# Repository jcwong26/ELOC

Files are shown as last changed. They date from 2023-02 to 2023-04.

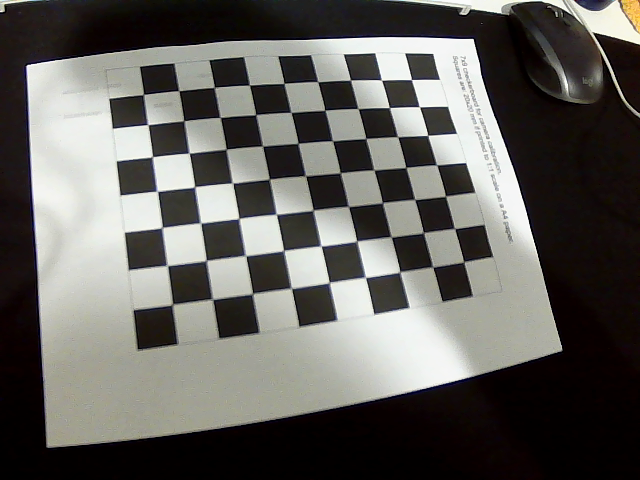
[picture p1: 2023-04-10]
camera_calibration/new_calibration_frames/calibration_frame_17.png

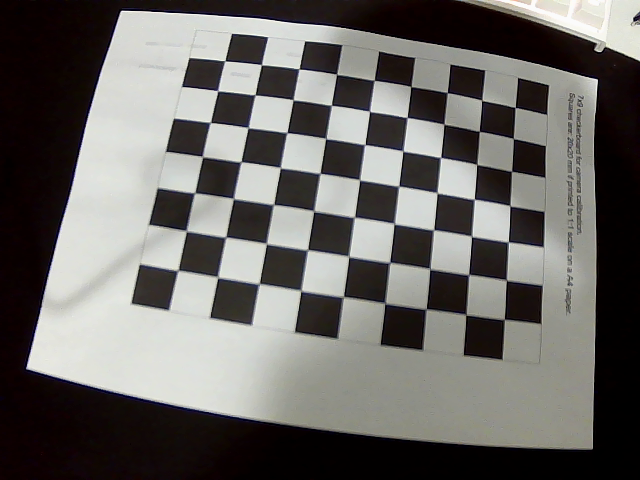
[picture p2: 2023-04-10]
camera_calibration/new_calibration_frames/calibration_frame_25.png

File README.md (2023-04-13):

# Energized Lock Out Container (ELOC)

ELOC is an e-bike storage solution to increase your range, without increasing your weight. With e-bikes becoming increasingly popular as a greener and healthier commuting option, our solution allows for charging of any e-bike so commuters do not have to worry about insufficient charge for their subsequent trips. ELOC features a fully autonomous process to load, lock, and charge your e-bike. With only the addition of a lightweight wireless power transfer adapter, our custom wireless charging technology provides enough power to charge a typical e-bike battery to 80% while securely locked throughout the day.

ELOC is a Capstone Design project made by four Mechatronics Engineering students at the University of Waterloo. 

For more details and a demo video check out our [website](https://mte481-group39-eloc.notion.site/mte481-group39-eloc/Energized-Lock-Out-Container-ELOC-88f4f57b00774851aa3dca28fe943a83)!

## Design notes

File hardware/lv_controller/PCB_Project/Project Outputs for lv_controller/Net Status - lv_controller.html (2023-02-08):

Altium customize

# Net Status Report

Date: | | 2022-11-29
Time: | | 10:16:27 PM
Elapsed Time: | | 00:00:00
Filename: | | C:\Users\dawso\OneDrive - University of Waterloo\4A\MTE481 - FYDP\LV Controller\PCB_Project\lv_controller.PcbDoc
Units: | | mmmils

Nets | Layer | Length
+3V3 | Signal Layers Only | 0mils
+5 | Signal Layers Only | 0mils
GND | Signal Layers Only | 0mils
GPIO17 | Signal Layers Only | 0mils
GPIO18 | Signal Layers Only | 0mils
GPIO21 | Signal Layers Only | 0mils
GPIO33 | Signal Layers Only | 0mils
GPIO34 | Signal Layers Only | 0mils
GPIO35 | Signal Layers Only | 0mils
GPIO36 | Signal Layers Only | 0mils
GPIO45 | Signal Layers Only | 0mils
GPIO46 | Signal Layers Only | 0mils
HSU_RX | Signal Layers Only | 0mils
HSU_TX | Signal Layers Only | 0mils
LIM_SW_1 | Signal Layers Only | 0mils
LIM_SW_2 | Signal Layers Only | 0mils
LIM_SW_3 | Signal Layers Only | 0mils
LIM_SW_4 | Signal Layers Only | 0mils
MCU_BOOT | Signal Layers Only | 0mils
MCU_EN | Signal Layers Only | 0mils
NetC18_2 | Signal Layers Only | 0mils
NetC19_2 | Signal Layers Only | 0mils
NetC20_2 | Signal Layers Only | 0mils
NetC24_2 | Signal Layers Only | 0mils
NetC25_2 | Signal Layers Only | 0mils
NetC26_2 | Signal Layers Only | 0mils
NetC4_1 | Signal Layers Only | 0mils
NetF1_2 | Signal Layers Only | 0mils
NetF2_2 | Signal Layers Only | 0mils
NetL5_1 | Signal Layers Only | 0mils
NetR10_2 | Signal Layers Only | 0mils
NetR11_1 | Signal Layers Only | 0mils
NetR12_1 | Signal Layers Only | 0mils
NetR4_2 | Signal Layers Only | 0mils
NetR7_2 | Signal Layers Only | 0mils
NetR8_1 | Signal Layers Only | 0mils
NetR9_1 | Signal Layers Only | 0mils
NetU1_12 | Signal Layers Only | 0mils
NetU1_15 | Signal Layers Only | 0mils
NetU1_17 | Signal Layers Only | 0mils
NetU1_18 | Signal Layers Only | 0mils
NetU1_19 | Signal Layers Only | 0mils
NetU1_20 | Signal Layers Only | 0mils
NetU1_34 | Signal Layers Only | 0mils
NetU1_35 | Signal Layers Only | 0mils
NetU1_4 | Signal Layers Only | 0mils
NetU1_5 | Signal Layers Only | 0mils
NetU1_6 | Signal Layers Only | 0mils
NetU1_7 | Signal Layers Only | 0mils
RING_LIGHT_DI_3V3 | Signal Layers Only | 0mils
RING_LIGHT_DI_5V | Signal Layers Only | 0mils
SOLENOID_N | Signal Layers Only | 0mils
SOLENOID_P | Signal Layers Only | 0mils
SOLENOID_UNLOCK_HIGH | Signal Layers Only | 0mils
USB_D_N | Signal Layers Only | 0mils
USB_D_P | Signal Layers Only | 0mils
VBUS | Signal Layers Only | 0mils

Back to top

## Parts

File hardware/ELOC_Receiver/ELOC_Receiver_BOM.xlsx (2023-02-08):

Comment | Description | Designator | Footprint | LibRef | Quantity | Arrow Part Number | Manufacturer Part Number | Part Number | PartNumber | Supplier Part Number 1 | Digi-Key_Part_Number_1 | Manufacturer_Part_Number | Manufacturer Part Number 1 | Mouser Part Number | Digi-Key_Part_Number_3 | Digi-Key_Part_Number_2
885012207078 | CAP CER 1UF 25V X7R 0805 | C1, C2, C3, C5 | FP-885012207078-MFG | CMP-207839-000010-1 | 4
C0805C104K1RACAUTO7210 | Capacitor | C4 | C0805 | C0805C104K1RACAUTO7210 | 1 | C0805C104K1RACAUTO7210 |  |  |  |  |  | C0805C104K1RACAUTO7210 |  | 80-C0805C104K1RAUTLR
CL21A106KOQNNNG | CL21 Series 0805 10uF 16V ±10% Tolerance X5R Multilayer Ceramic Chip Capacitor | C6, C7 | FP-CL21-IPC_C | CMP-13271-002240-1 | 2
08055D104KAT2A |  | C8 | CAPC2013X140X50ML20T25 | CMP-2007-04689-1 | 1 |  |  | 08055D104KAT2A
CL21B334KBFNNNE | CAP CER 0.33UF 50V X7R 0805 | C9 | FP-CL21-F-IPC_C | CMP-13271-000003-1 | 1 |  | CL21B334KBFNNNE
CL21A106KOQNNNE | CL21 Series 0805 10uF 16V ±10% Tolerance X5R Multilayer Ceramic Chip Capacitor | C10 | FP-CL21-IPC_B | CMP-2000-06102-2 | 1
CL21A226MQQNNNG | CL21 Series 0805 22uF 6.3V ±20% Tolerance X5R Multilayer Ceramic Chip Capacitor | C11 | FP-CL21-IPC_B | CMP-13271-002967-1 | 1
UCD1K470MNL1GS | Capacitor Polarised | C12, C13 | CAPAE1030X1080N | UCD1K470MNL1GS | 2 | UCD1K470MNL1GS |  |  |  |  |  | UCD1K470MNL1GS |  | 647-UCD1K470MNL1GS
C0805C104K5RACTU | CAP CER 0.1UF 50V X7R 0805 | C14, C23, C24, C25 | CAP0805 | C0805C104K5RACTU | 4 |  |  |  |  | 399-1170-1-ND
C1206C103JAGECAUTO | Capacitor | C15, C16, C17, C18, C19, C20 | CAPC3216X110N | C1206C103JAGECAUTO | 6 | C1206C103JAGECAUTO |  |  |  |  |  | C1206C103JAGECAUTO |  | 80-C1206C103JAGECAUT
GRM21BR71C105KA01L | CAP CER 1UF 16V X7R 0805 | C21 | CAP0805 | GRM21BR71C105KA01L | 1 |  |  |  |  | 490-1691-1-ND
CL21A226MOCLRNC | CAP CER 22UF 16V X5R 0805 | C22 | CAP0805 | CL21A226MOCLRNC | 1 |  |  |  |  | 1276-6780-1-ND
12V | LED GREEN CLEAR 0603 SMD | D1 | FP-150060VS75000-MFG | CMP-1426-00006-5 | 1
5V | LED GREEN CLEAR 0603 SMD | D2 | FP-150060VS75000-MFG | CMP-1426-00006-5 | 1
3V3 | LED GREEN CLEAR 0603 SMD | D3 | FP-150060VS75000-MFG | CMP-1426-00006-5 | 1
1SMB5947BT3G | 3 W Zener Voltage Regulator, 2-Pin SMB, Pb-Free, Tape and Reel | D4, D5, D6 | ONSC-SMB-2-403A-03_H_V | CMP-1060-00168-1 | 3 |  |  |  | 1SMB5947BT3G
MBR5U100-TP | Schottky Diode | D7, D12 | MBR5U100TP | MBR5U100-TP | 2 |  |  |  |  |  |  | MBR5U100-TP
STPS4S200UFN | Schottky Diode | D8, D9, D10, D11, D13, D14, D15, D16 | SODFL5436X110N | STPS4S200UFN | 8 | STPS4S200UFN |  |  |  |  |  | STPS4S200UFN |  | 511-STPS4S200UFN
D_PMEG3050EP,115 | DIODE SCHOTTKY 360mV 30V 5A | D17 | SOD-128 | D_PMEG3050EP,115 | 1
MP4541GN-Z | Integrated Circuit | IC1 | SOIC127P600X170-9N | MP4541GN-Z | 1 |  |  |  |  |  |  | MP4541GN-Z |  | 946-MP4541GN-Z
AS78L05RTR-E1 | Integrated Circuit | IC2 | DIODES_SOT-89 | AS78L05RTR-E1 | 1 | AS78L05RTR-E1 |  |  |  |  |  | AS78L05RTR-E1 |  | 621-AS78L05RTR-E1
691137710002 | Series 1377 - 5.00 mm Horizontal Entry with Pressure Clamp WR-TBL, 2 pin | J1, J2 | 691137710002 | CMP-1502-03324-1 | 2 |  |  | 691137710002
USB4105-GF-A | No Description Available | J3 | USB4105_GCT | USB4105-GF-A | 1 |  |  |  |  |  | 2073-USB4105-GF-ACT-ND | USB4105-GF-A |  |  | 2073-USB4105-GF-ATR-ND | 2073-USB4105-GF-ADKR-ND
61301611821 | THT Vertical Socket Header WR-PHD, Pitch 2.54 mm, Single Row, 16 pins | J4 | 61301611821 | CMP-1502-01343-1 | 1 |  |  | 61301611821
ALQ112 | LQ Relays, 12 V Coil Voltage, 400 mW Nominal Operating Power, -40 to 85 degC, 5-Pin LQ, Carton, Case, RoHS | K1 | PNSC-LQ-5-2000x1000x1600_V | CMP-1503-00193-1 | 1 |  |  |  | ALQ112
LBR2518T100K | SMD Inductors 10uH ±10% 0.235A 0.247Ω 1007 | L1 | FP-LB2518-1_8-0_2-IPC_A | CMP-14484-000483-1 | 1
SDR1307-180ML | Inductor | L2 | SDR1307-220ML | SDR1307-180ML | 1 | SDR1307-180ML |  |  |  |  |  | SDR1307-180ML |  | 652-SDR1307-180ML
T2N7002BK,LM | MOSFET (N-Channel) | Q1 | TBAT54CLM | T2N7002BK,LM | 1 | T2N7002BK,LM |  |  |  |  |  | T2N7002BK,LM |  | 757-T2N7002BKLM
RMCF0805JT10K0 | 10kΩ ±5% 0.125W 0805 Thick Film Chip Resistor AEC-Q200 compliant | R1, R7 | FP-RMCF0805-IPC_A | CMP-26527-002663-1 | 2
CRCW080580K6FKEA | RES Thick Film, 80.6kΩ, 1%, 0.125W, 100ppm/°C, 0805 | R2 | FP-CRCW0805-e3-IPC_A | CMP-2001-04127-2 | 1
RMCF0805FT110K | 110kΩ ±1% 0.125W 0805 Thick Film Chip Resistor AEC-Q200 compliant | R3 | FP-RMCF0805-IPC_C | CMP-26527-000712-1 | 1
RNCP0805FTD1K00 | 1kΩ ±1% 0.25W 0805 High Power Anti-Sulfur Thin Film Chip Resistor | R4, R5, R6 | FP-RNCP0805-MFG | CMP-26527-001902-1 | 3
SHUNT | Resistor | R8 | RESC6434X90N | CRA2512-FZ-R010ELF | 1 | CRA2512-FZ-R010ELF |  |  |  |  |  | CRA2512-FZ-R010ELF |  | 652-CRA2512FZR010ELF
SMF51K0JT | RES SMD 1K OHM 5% 5W 5329 | R9, R10 | FP-SMF5-MFG | CMP-03211-011405-1 | 2
RC0805FR-0710KL | RES SMD 10K OHM 1% 1/8W 0805 | R11, R16, R17, R18 | RES0805 | RC0805FR-0710KL | 4 |  |  |  |  | 311-10.0KCRCT-ND
CRCW08055K10FKEA | RES Thick Film, 5.1kΩ, 1%, 0.125W, 100ppm/°C, 0805 | R12, R13 | FP-CRCW0805-e3-MFG | CMP-2001-04024-2 | 2
RC0805FR-07267KL |  | R14, R15 | RESC2013X60X35NL10T20 | CMP-2001-01033-1 | 2 |  |  | RC0805FR-07267KL
RESET | Tactile Button_3X6X2 | S1 | Tactile_Button_3X6X2 | Tactile Button_3X6X2 | 1
BOOT | Tactile Button_3X6X2 | S2 | Tactile_Button_3X6X2 | Tactile Button_3X6X2 | 1
GND | PC TEST POINT MINIATURE WHITE | TP1 | TESTPOINT_LOOP | TESTPOINT_LOOP | 1 |  |  |  |  | 36-5002-ND |  |  | 5002
12V | PC TEST POINT MINIATURE WHITE | TP2 | TESTPOINT_LOOP | TESTPOINT_LOOP | 1 |  |  |  |  | 36-5002-ND |  |  | 5002
5V | PC TEST POINT MINIATURE WHITE | TP3 | TESTPOINT_LOOP | TESTPOINT_LOOP | 1 |  |  |  |  | 36-5002-ND |  |  | 5002
3V3 | PC TEST POINT MINIATURE WHITE | TP4 | TESTPOINT_LOOP | TESTPOINT_LOOP | 1 |  |  |  |  | 36-5002-ND |  |  | 5002
AZ1117IH-3.3TRG1 | IC REG LINEAR 3.3V 1A SOT223 | U1 | FP-SOT223-IPC_B | CMP-12756-000043-1 | 1
INA180A1IDBVR | IC CURR SENSE 1 CIRCUIT SOT23-5 | U2 | FP-DBV0005A-IPC_A | CMP-04895-000140-1 | 1
ESP32-S2-SOLO-U-N4 | WiFi Modules - 802.11 SMD module, ESP32-S2, 4 MB SPI flash, IPEX antenna | U3 | ESP32S2SOLOUN4 | ESP32-S2-SOLO-U-N4 | 1 |  |  |  |  |  |  | ESP32-S2-SOLO-U-N4 |  | 356-ESP32-S2-SOLOUN4
TC33X-2-203E | Variable Resistor | VR1 | TC33X2503E | TC33X-2-203E | 1 | TC33X-2-203E |  |  |  |  |  | TC33X-2-203E |  | 652-TC33X-2-203E

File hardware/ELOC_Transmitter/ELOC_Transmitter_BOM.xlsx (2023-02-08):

Comment | Description | Designator | Footprint | LibRef | Quantity | Arrow Part Number | Digi-Key_Part_Number_1 | Digi-Key_Part_Number_2 | Digi-Key_Part_Number_3 | Manufacturer Part Number | Manufacturer Part Number 1 | Manufacturer_Part_Number | Mouser Part Number | Part Number | Supplier Part Number 1
885012207078 | CAP CER 1UF 25V X7R 0805 | C1, C2 | FP-885012207078-MFG | CMP-207839-000010-1 | 2
C0805C104K1RACAUTO7210 | Capacitor | C3, C4 | C0805 | C0805C104K1RACAUTO7210 | 2 | C0805C104K1RACAUTO7210 |  |  |  |  |  | C0805C104K1RACAUTO7210 | 80-C0805C104K1RAUTLR
C1206C103JAGECAUTO | Capacitor | C5, C6, C7, C8, C9, C10 | CAPC3216X110N | C1206C103JAGECAUTO | 6 | C1206C103JAGECAUTO |  |  |  |  |  | C1206C103JAGECAUTO | 80-C1206C103JAGECAUT
C0805C104K5RACTU | CAP CER 0.1UF 50V X7R 0805 | C11, C14, C17, C18, C30, C32 | CAP0805 | C0805C104K5RACTU | 6 |  |  |  |  |  |  |  |  |  | 399-1170-1-ND
860010573007 | Capacitor Polarised | C12, C13, C21, C22, C23 | CAPPRD250W52D630H1250 | 860010573007 | 5 |  |  |  |  |  |  | 860010573007 | 710-860010573007
CL21A226MOCLRNC | CAP CER 22UF 16V X5R 0805 | C15, C24, C29, C31 | CAP0805 | CL21A226MOCLRNC | 4 |  |  |  |  |  |  |  |  |  | 1276-6780-1-ND
CL21B334KBFNNNE | CAP CER 0.33UF 50V X7R 0805 | C16, C20 | FP-CL21-F-IPC_C | CMP-13271-000003-1 | 2 |  |  |  |  | CL21B334KBFNNNE
08055D104KAT2A |  | C19 | CAPC2013X140X50ML20T25 | CMP-2007-04689-1 | 1 |  |  |  |  |  |  |  |  | 08055D104KAT2A
CL21B472KBANNNC | CL21 Series 0805 4.7nF 50V ±10% Tolerance X7R Multilayer Ceramic Chip Capacitor | C25 | FP-CL21-IPC_A | CMP-13271-001405-1 | 1
CL21A106KOQNNNE | CL21 Series 0805 10uF 16V ±10% Tolerance X5R Multilayer Ceramic Chip Capacitor | C26 | FP-CL21-IPC_B | CMP-2000-06102-2 | 1
CL21A226MQQNNNG | CL21 Series 0805 22uF 6.3V ±20% Tolerance X5R Multilayer Ceramic Chip Capacitor | C27 | FP-CL21-IPC_B | CMP-13271-002967-1 | 1
GRM21BR71C105KA01L | CAP CER 1UF 16V X7R 0805 | C28 | CAP0805 | GRM21BR71C105KA01L | 1 |  |  |  |  |  |  |  |  |  | 490-1691-1-ND
1N4148WS | DIODE GEN PURP 75V 150MA SOD323F | D1, D2, D3, D4, D5, D6 | FP-477AB-IPC_C | CMP-07163-000040-1 | 6
150060VS75000 | LED GREEN CLEAR 0603 SMD | D7, D10, D11, D12 | FP-150060VS75000-MFG | CMP-1426-00006-5 | 4
SK86L-TP | Schottky Diode | D8, D9 | DIOM7959X262N | SK86L-TP | 2 | SK86L-TP |  |  |  |  |  | SK86L-TP | 833-SK86L-TP
D_PMEG3050EP,115 | DIODE SCHOTTKY 360mV 30V 5A | D13 | SOD-128 | D_PMEG3050EP,115 | 1
NCP5104DR2G | Integrated Circuit | IC1, IC2 | SOIC127P600X175-8N | NCP5104DR2G | 2 | NCP5104DR2G |  |  |  |  |  | NCP5104DR2G | 863-NCP5104DR2G
MP3426DL-LF-Z | Integrated Circuit | IC3 | SON50P300X400X100-15N-D | MP3426DL-LF-Z | 1 |  |  |  |  |  |  | MP3426DL-LF-Z | 946-MP3426DL-LF-Z
AS78L05RTR-E1 | Integrated Circuit | IC4 | DIODES_SOT-89 | AS78L05RTR-E1 | 1 | AS78L05RTR-E1 |  |  |  |  |  | AS78L05RTR-E1 | 621-AS78L05RTR-E1
691137710002 | Series 1377 - 5.00 mm Horizontal Entry with Pressure Clamp WR-TBL, 2 pin | J1, J2 | 691137710002 | CMP-1502-03324-1 | 2 |  |  |  |  |  |  |  |  | 691137710002
USB4105-GF-A | No Description Available | J3 | USB4105_GCT | USB4105-GF-A | 1 |  | 2073-USB4105-GF-ACT-ND | 2073-USB4105-GF-ADKR-ND | 2073-USB4105-GF-ATR-ND |  |  | USB4105-GF-A
PR20203VBNN | CONN HEADER VERT 3POS 2.54MM | J4 | FP-PR20203VBNN-MFG | CMP-77940-000002-1 | 1 |  |  |  |  | PR20203VBNN
SRP1265C-100M | FIXED IND 10UH 12A 18 MOHM SMD | L1 | FP-SRP1265C-MFG | CMP-07248-000045-1 | 1 |  |  |  |  |  |  |  |  | SRP1265C-100M
AOD4184A | MOSFET N-CH 40V 50A TO252 | Q1, Q2, Q3, Q4 | FP-TO252-MFG | CMP-83955-000007-1 | 4
T2N7002BK,LM | MOSFET (N-Channel) | Q5 | TBAT54CLM | T2N7002BK,LM | 1 | T2N7002BK,LM |  |  |  |  |  | T2N7002BK,LM | 757-T2N7002BKLM
RMCF1206FT4R02 | Resistor | R1, R2, R3, R4, R5, R6, R7, R8, R9, R10, R11, R12 | RESC3216X70N | RMCF1206FT4R02 | 12 | RMCF1206FT4R02 |  |  |  |  |  | RMCF1206FT4R02
RNCP0805FTD1K00 | 1kΩ ±1% 0.25W 0805 High Power Anti-Sulfur Thin Film Chip Resistor | R13, R17, R18, R19 | FP-RNCP0805-MFG | CMP-26527-001902-1 | 4
RC0805FR-0710KL | RES SMD 10K OHM 1% 1/8W 0805 | R14, R22, R23, R26, R28, R29 | RES0805 | RC0805FR-0710KL | 6 |  |  |  |  |  |  |  |  |  | 311-10.0KCRCT-ND
SHUNT | Resistor | R15 | RESC6434X90N | CRA2512-FZ-R010ELF | 1 | CRA2512-FZ-R010ELF |  |  |  |  |  | CRA2512-FZ-R010ELF | 652-CRA2512FZR010ELF
ERJ-6ENF6652V |  | R16 | RESC2013X70X40LL20T20 | CMP-2001-00269-1 | 1 |  |  |  |  |  |  |  |  | ERJ-6ENF6652V
ERJ-6ENF1873V |  | R20, R27 | RESC2013X70X40NL20T20 | CMP-1013-00765-2 | 2 |  |  |  |  |  |  |  |  | ERJ-6ENF1873V
RNCP0805FTD12K1 | 12.1kΩ ±1% 0.25W 0805 High Power Anti-Sulfur Thin Film Chip Resistor | R21 | FP-RNCP0805-IPC_B | CMP-26527-004331-1 | 1
CRCW08055K10FKEA | RES Thick Film, 5.1kΩ, 1%, 0.125W, 100ppm/°C, 0805 | R24, R25 | FP-CRCW0805-e3-MFG | CMP-2001-04024-2 | 2
RESET | Tactile Button_3X6X2 | S1 | Tactile_Button_3X6X2 | Tactile Button_3X6X2 | 1
BOOT | Tactile Button_3X6X2 | S2 | Tactile_Button_3X6X2 | Tactile Button_3X6X2 | 1
Bridge 1 | PC TEST POINT MINIATURE WHITE | TP1 | TESTPOINT_LOOP | TESTPOINT_LOOP | 1 |  |  |  |  |  | 5002 |  |  |  | 36-5002-ND
Bridge 2 | PC TEST POINT MINIATURE WHITE | TP2 | TESTPOINT_LOOP | TESTPOINT_LOOP | 1 |  |  |  |  |  | 5002 |  |  |  | 36-5002-ND
Oscillator Out | PC TEST POINT MINIATURE WHITE | TP3 | TESTPOINT_LOOP | TESTPOINT_LOOP | 1 |  |  |  |  |  | 5002 |  |  |  | 36-5002-ND
NOT Oscillator Out | PC TEST POINT MINIATURE WHITE | TP4 | TESTPOINT_LOOP | TESTPOINT_LOOP | 1 |  |  |  |  |  | 5002 |  |  |  | 36-5002-ND
GND | PC TEST POINT MINIATURE WHITE | TP5 | TESTPOINT_LOOP | TESTPOINT_LOOP | 1 |  |  |  |  |  | 5002 |  |  |  | 36-5002-ND
12V | PC TEST POINT MINIATURE WHITE | TP6, TP7 | TESTPOINT_LOOP | TESTPOINT_LOOP | 2 |  |  |  |  |  | 5002 |  |  |  | 36-5002-ND
24V | PC TEST POINT MINIATURE WHITE | TP8, TP9 | TESTPOINT_LOOP | TESTPOINT_LOOP | 2 |  |  |  |  |  | 5002 |  |  |  | 36-5002-ND
5V | PC TEST POINT MINIATURE WHITE | TP10 | TESTPOINT_LOOP | TESTPOINT_LOOP | 1 |  |  |  |  |  | 5002 |  |  |  | 36-5002-ND
3V3 | PC TEST POINT MINIATURE WHITE | TP11 | TESTPOINT_LOOP | TESTPOINT_LOOP | 1 |  |  |  |  |  | 5002 |  |  |  | 36-5002-ND
SN74LVC1G14DBVR | Single Schmitt-Trigger Inverter, DBV0005A, LARGE T&R | U1 | DBV0005A_L | CMP-0859-00030-4 | 1
INA180A1IDBVR | IC CURR SENSE 1 CIRCUIT SOT23-5 | U2 | FP-DBV0005A-IPC_A | CMP-04895-000140-1 | 1
AZ1117IH-3.3TRG1 | IC REG LINEAR 3.3V 1A SOT223 | U3 | FP-SOT223-IPC_B | CMP-12756-000043-1 | 1
ESP32-S2-SOLO-U-N4 | WiFi Modules - 802.11 SMD module, ESP32-S2, 4 MB SPI flash, IPEX antenna | U4 | ESP32S2SOLOUN4 | ESP32-S2-SOLO-U-N4 | 1 |  |  |  |  |  |  | ESP32-S2-SOLO-U-N4 | 356-ESP32-S2-SOLOUN4

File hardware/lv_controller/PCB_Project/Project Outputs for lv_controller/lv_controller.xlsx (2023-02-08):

Comment | Description | Designator | Footprint | LibRef | Quantity
SS2FH10-M3/H, 100V @ 2A | No Description Available | CR1 | CR_10-M3/H_VIS | SS2FH10-M3/H | 1
C1F-8 | C1F 8 (0685F8000-01) | 1206 SMT Fuse | Fast Acting | 8A | F1, F2 | FUSC3215X83N | C1F-8 | 2
USB4105-GF-A | No Description Available | J1 | USB4105_GCT | USB4105-GF-A | 1
RLB0913-2R2K, 2.2uH Inductor, 5.6A |  | L5 | RLB0913-4R7K_BRN | RLB0913-4R7K | 1
NTD14N03RT4G | Power MOSFET, 14 A, 25 V, N-Channel, 3-Pin DPAK, Pb-Free, Tape and Reel | Q1 | ONSC-DPAK-3-369C-01_V | CMP-1058-00361-1 | 1
TS02-66-60-BK-260-LCR-D | 6 x 6 mm, 6 mm Actuator Height, 260 gf, Black, Long Crimped, Through Hole, SPST, Tactile Switch | S1, S2 | SW_TS02-66-60-BK-260-LCR-D | TS02-66-60-BK-260-LCR-D | 2
ESP32-S2-SOLO-U-N4 | WiFi 802.11b/g/n Transceiver Module 2.4GHz PCB Trace + IPEX Surface Mount | U1 | XCVR_ESP32-S2-SOLO-U-N4R2 | ESP32-S2-SOLO-U-N4R2 | 1
TPS566242DRLR | No Description Available | U2 | SOT5x3_DRL_TEX | TPS566242DRLR | 1
BD33HC5WEFJ-E2 | No Description Available | U3 | HTSOP-J8_ROM | BD33HC5WEFJ-E2 | 1
L9958 | Bipolar Motor Driver CMOS SPI PowerSO-16â„¢ | U4, U5 | SOIC127P1420X360-21N | L9958 | 2
TXS0101DCKR | No Description Available | U6 | DCK0006A_N | TXS0101DCKR | 1

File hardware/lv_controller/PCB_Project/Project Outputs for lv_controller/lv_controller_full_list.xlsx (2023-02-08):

Comment | Description | Designator | Footprint | LibRef | Quantity | PartNumber | Application_BuildNumber | DocumentNumber | Manufacturer_Part_Number | Number of contacts
SS2FH10-M3/H, 100V @ 2A | No Description Available | CR1 | CR_10-M3/H_VIS | SS2FH10-M3/H | 1 | SS2FH10-M3/HGICT-ND |  |  | SS2FH10-M3/H
C1F-8 | C1F 8 (0685F8000-01) | 1206 SMT Fuse | Fast Acting | 8A | F1, F2 | FUSC3215X83N | C1F-8 | 2 | 507-1889-1-ND
USB4105-GF-A | No Description Available | J1 | USB4105_GCT | USB4105-GF-A | 1 | 2073-USB4105-GF-ACT-ND |  |  | USB4105-GF-A
RLB0913-2R2K, 2.2uH Inductor, 5.6A |  | L5 | RLB0913-4R7K_BRN | RLB0913-4R7K | 1 | RLB0913-4R7K-ND |  |  | RLB0913-4R7K
NTD14N03RT4G | Power MOSFET, 14 A, 25 V, N-Channel, 3-Pin DPAK, Pb-Free, Tape and Reel | Q1 | ONSC-DPAK-3-369C-01_V | CMP-1058-00361-1 | 1 | NTD14N03RT4GOSCT-ND
TS02-66-60-BK-260-LCR-D | 6 x 6 mm, 6 mm Actuator Height, 260 gf, Black, Long Crimped, Through Hole, SPST, Tactile Switch | S1, S2 | SW_TS02-66-60-BK-260-LCR-D | TS02-66-60-BK-260-LCR-D | 2 | 2223-TS02-66-60-BK-260-LCR-D-ND
ESP32-S2-SOLO-U-N4 | WiFi 802.11b/g/n Transceiver Module 2.4GHz PCB Trace + IPEX Surface Mount | U1 | XCVR_ESP32-S2-SOLO-U-N4R2 | ESP32-S2-SOLO-U-N4R2 | 1 | 1965-ESP32-S2-SOLO-U-N4CT-ND
TPS566242DRLR | No Description Available | U2 | SOT5x3_DRL_TEX | TPS566242DRLR | 1 | 296-TPS566242DRLRCT-ND |  |  | TPS566242DRLR
BD33HC5WEFJ-E2 | No Description Available | U3 | HTSOP-J8_ROM | BD33HC5WEFJ-E2 | 1 | BD33HC5WEFJ-E2CT-ND |  |  | BD33HC5WEFJ-E2
L9958 | Bipolar Motor Driver CMOS SPI PowerSO-16â„¢ | U4, U5 | SOIC127P1420X360-21N | L9958 | 2 | 497-11626-5-ND
TXS0101DCKR | No Description Available | U6 | DCK0006A_N | TXS0101DCKR | 1 | 296-22864-1-ND |  |  | TXS0101DCKR
12V Solenoid Lock |  |  |  |  | 1 | 1528-5065-ND |  |  | 5065
Limit Switch | SWITCH SNAP ACT SPST-NO 3A 125V |  |  |  | 4 | Z6377-ND |  |  | SS-3FL111P-3T

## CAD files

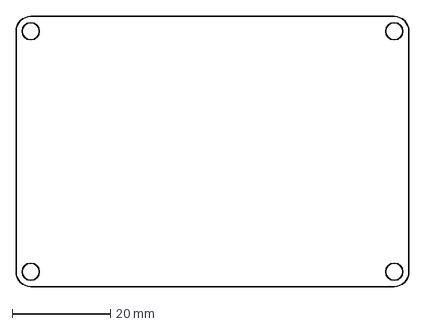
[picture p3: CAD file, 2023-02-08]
hardware/ELOC_Receiver/receiver_board_outline.dxf
80.0 x 55.0 mm

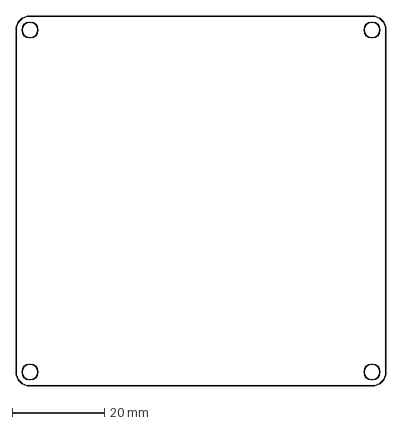
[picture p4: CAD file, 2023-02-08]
hardware/ELOC_Transmitter/transmitter_board_outline.dxf
80.0 x 80.0 mm

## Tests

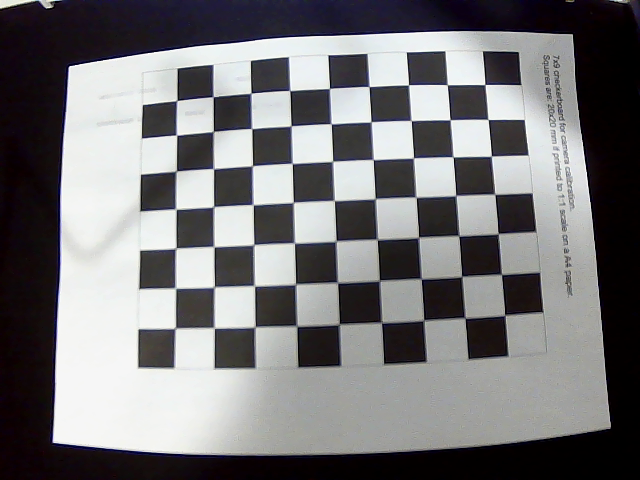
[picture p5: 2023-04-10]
camera_calibration/new_calibration_frames/calibration_frame_18.png

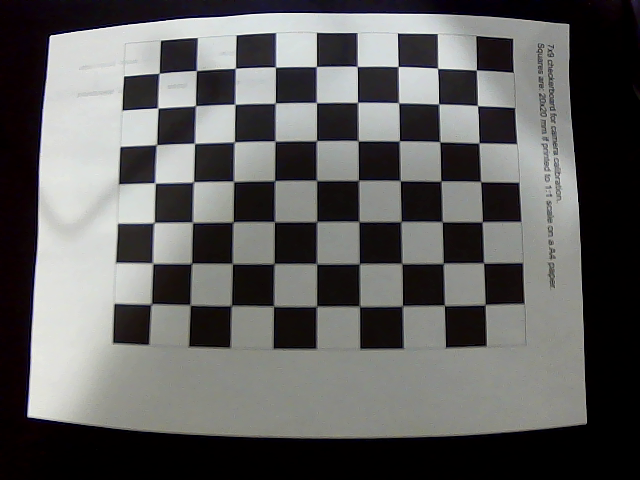
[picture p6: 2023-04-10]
camera_calibration/new_calibration_frames/calibration_frame_10.png

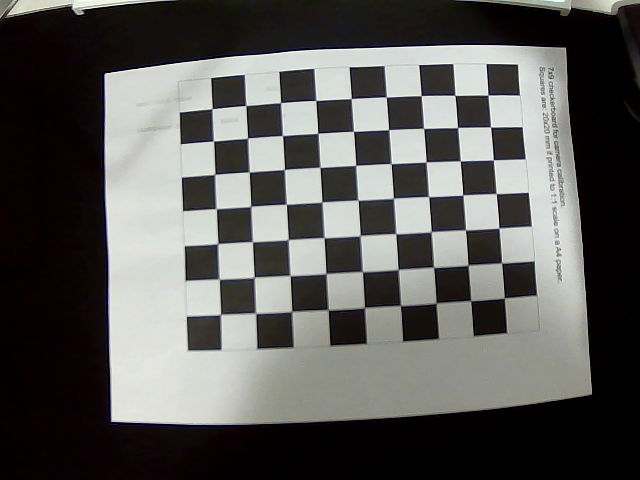
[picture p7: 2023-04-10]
camera_calibration/new_calibration_frames/calibration_frame_21.png

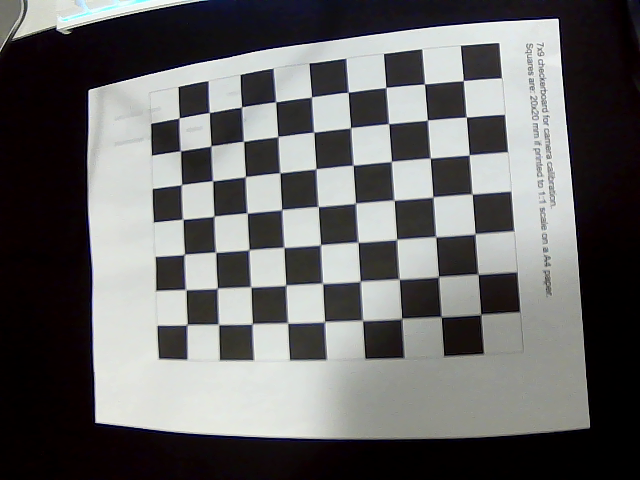
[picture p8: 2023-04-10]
camera_calibration/new_calibration_frames/calibration_frame_23.png

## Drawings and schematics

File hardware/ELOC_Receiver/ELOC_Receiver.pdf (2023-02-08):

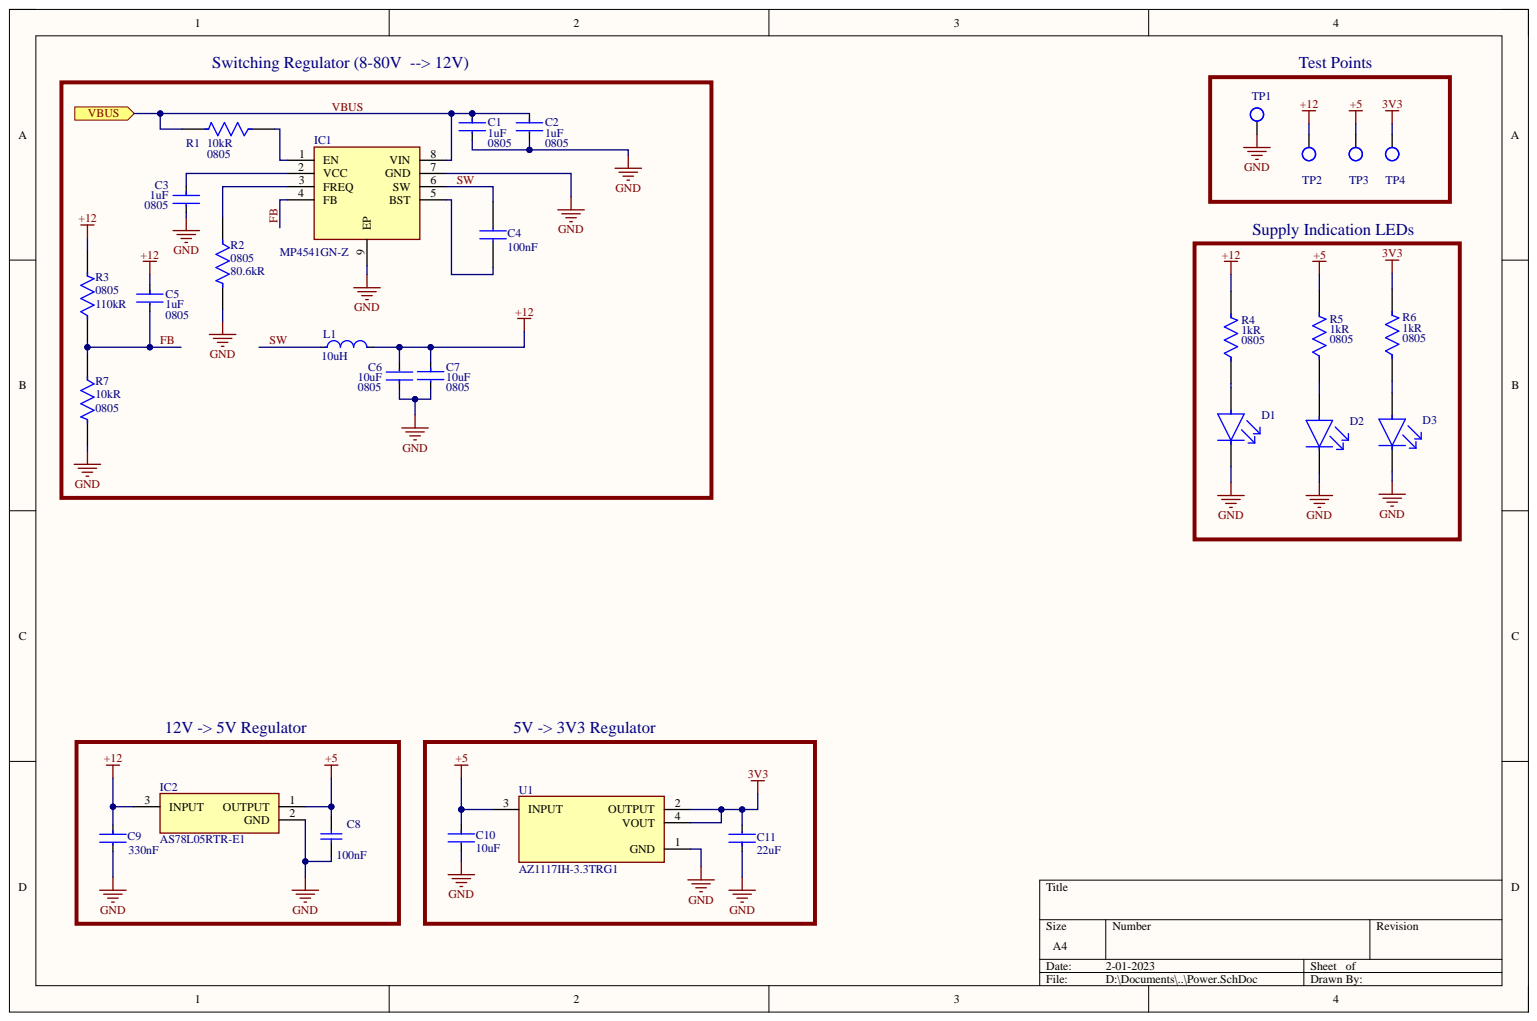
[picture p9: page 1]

3 | | 6 | SW

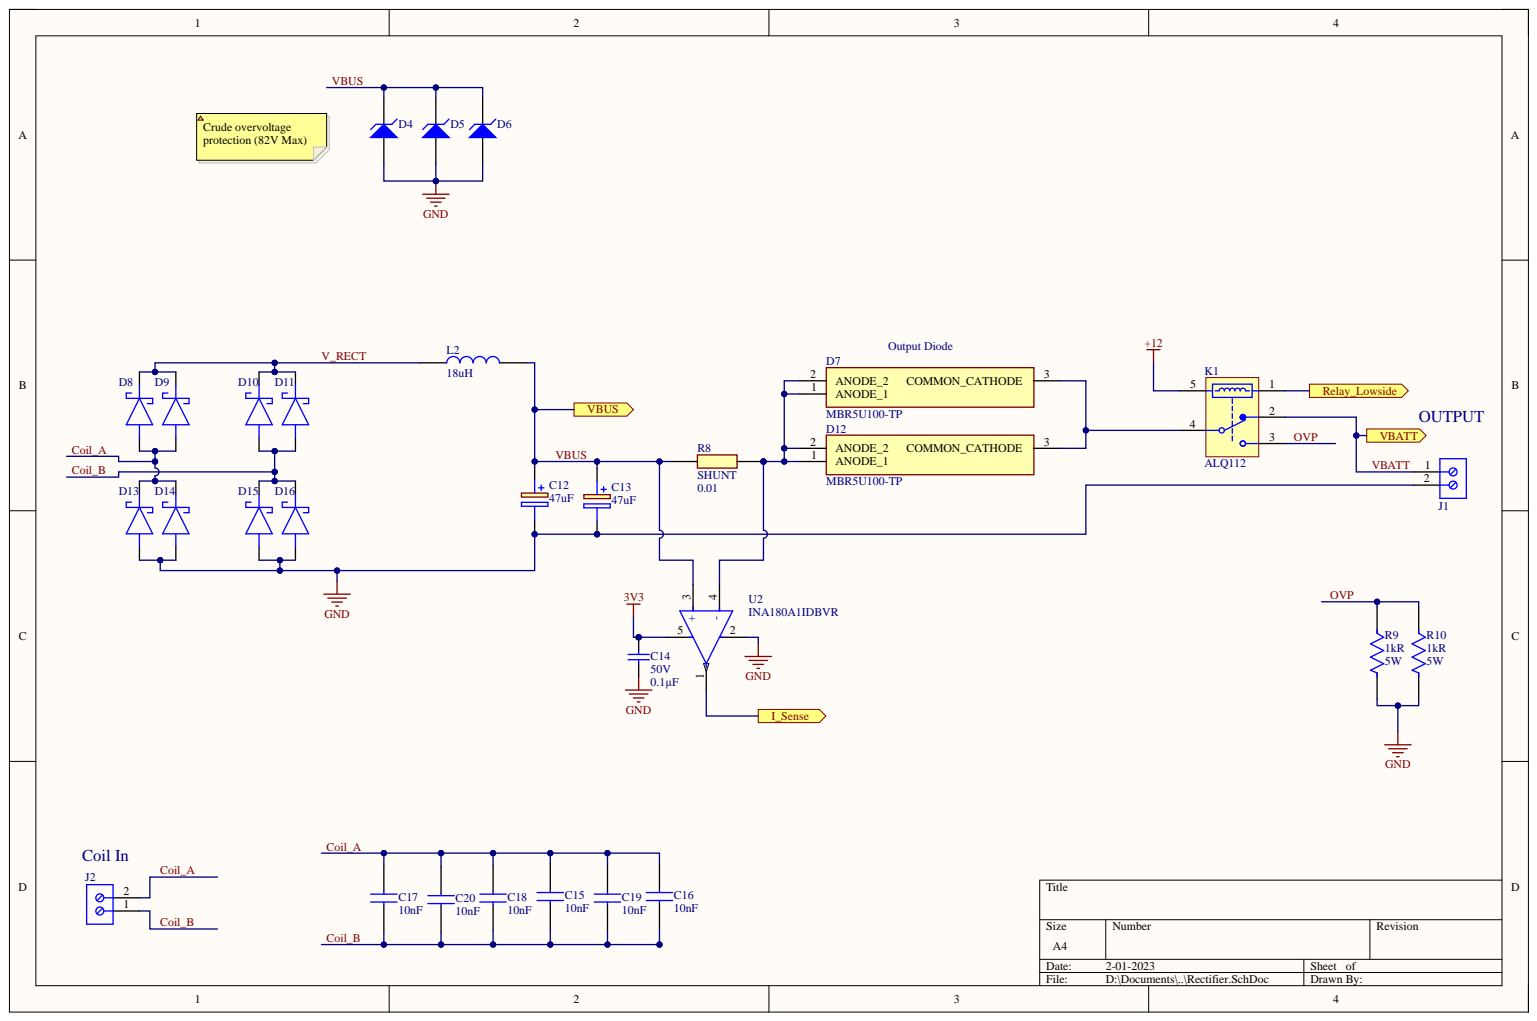
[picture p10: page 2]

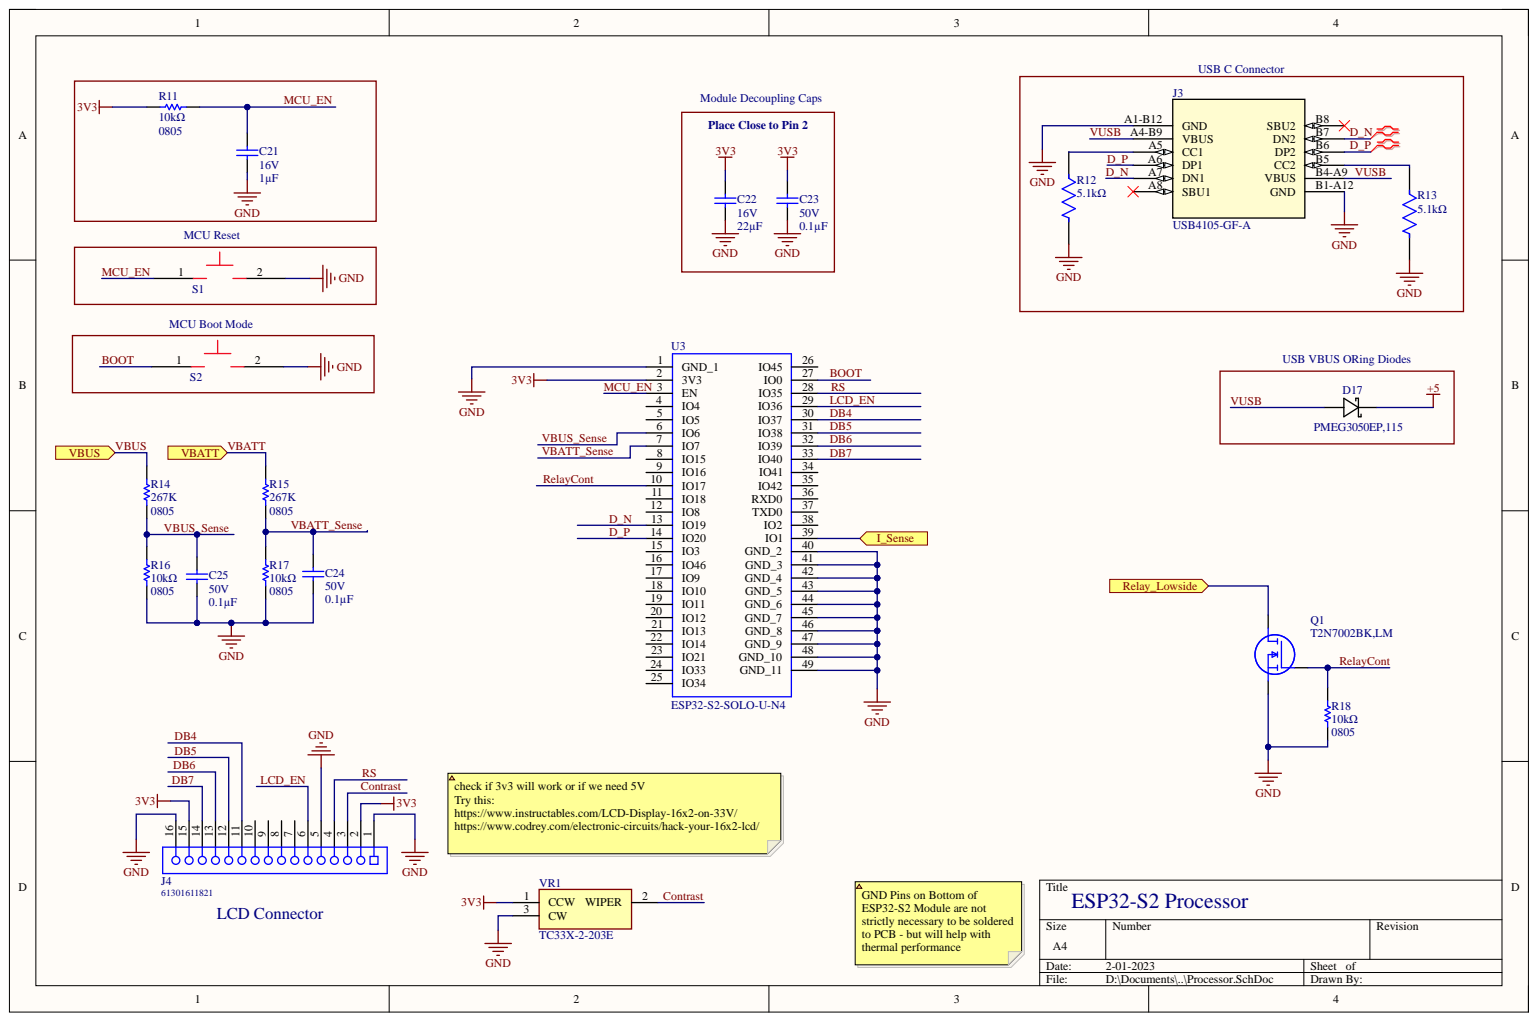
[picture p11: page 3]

Place Close to Pin 2 10kΩ

VBUS_Sense | IO7 7
VBATT_Sense | IO15 8

check if 3v3 will work or if we need 5V
Try this:
https://www.instructables.com/LCD-Display-16x2-on-33V/
https://www.codrey.com/electronic-circuits/hack-your-16x2-lcd/

GND Pins on Bottom of
ESP32-S2 Module are not
strictly necessary to be soldered
to PCB - but will help with
thermal performance

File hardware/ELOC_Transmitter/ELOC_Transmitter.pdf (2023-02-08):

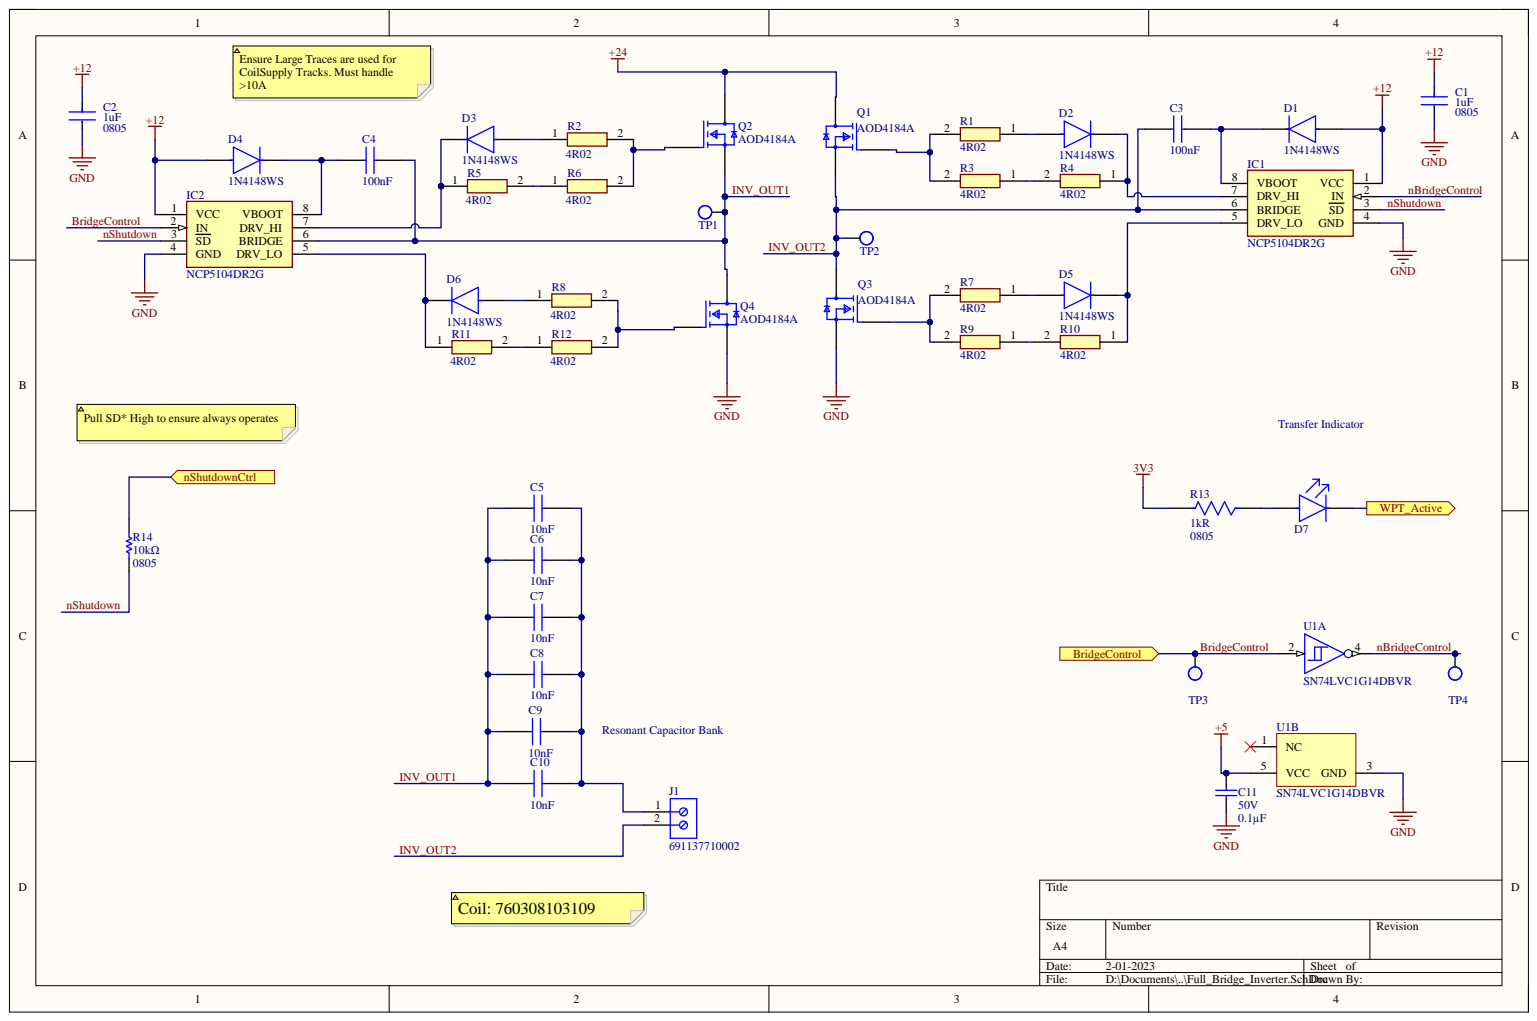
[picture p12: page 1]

Ensure Large Traces are used for
CoilSupply Tracks. Must handle

Pull SD* High to ensure always operates

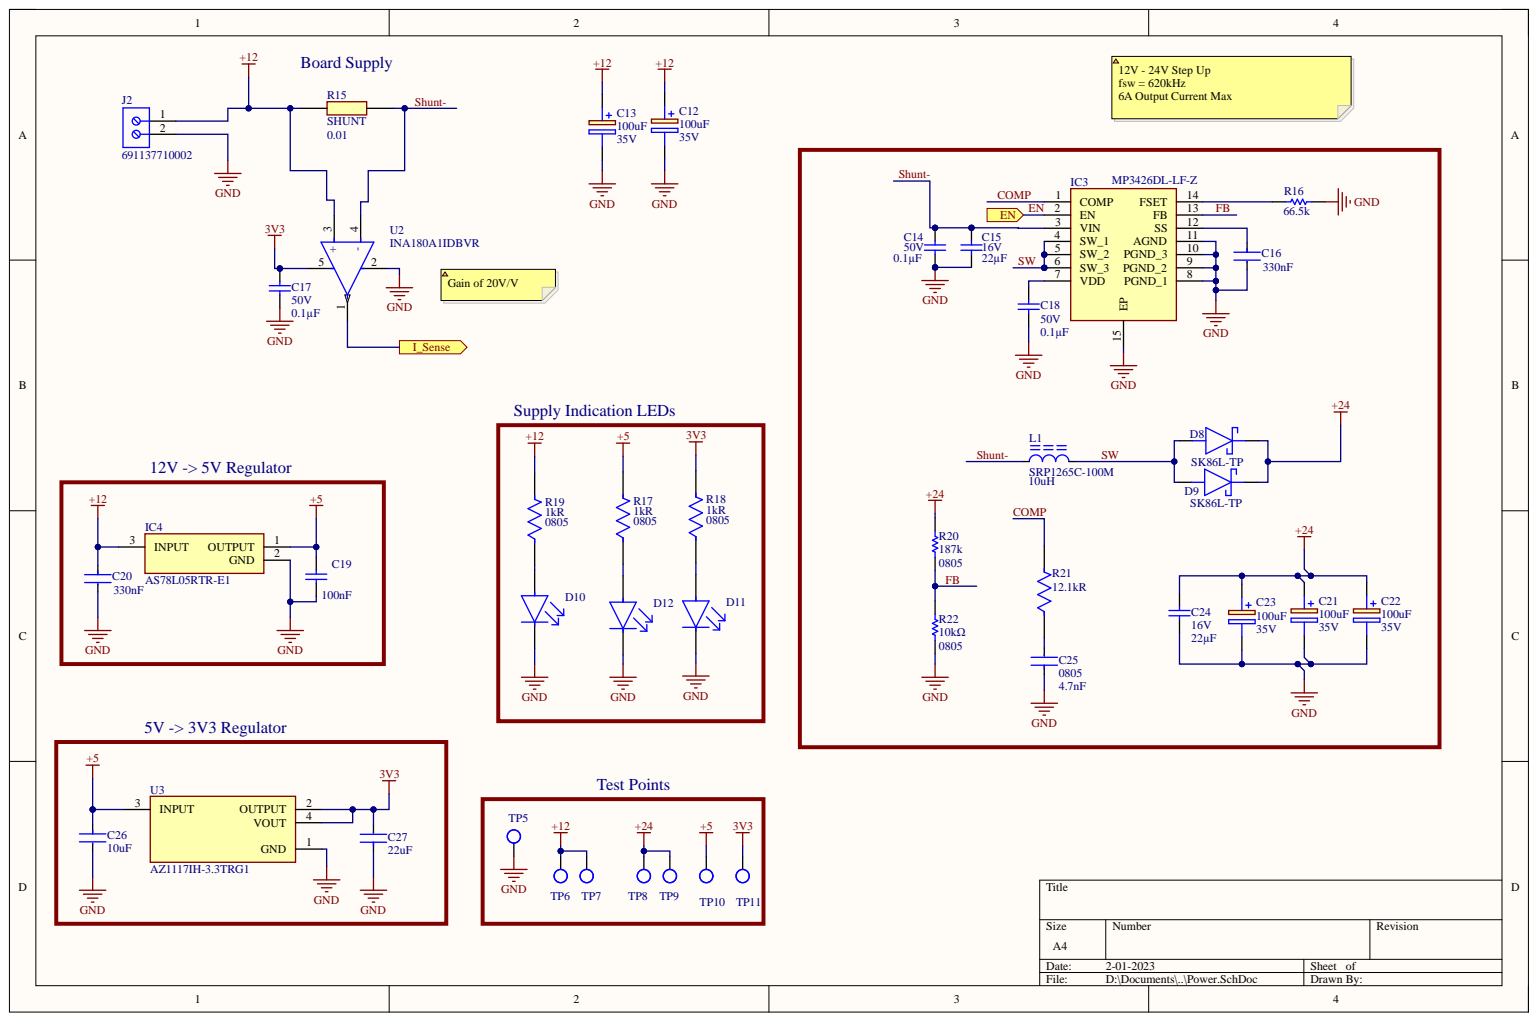
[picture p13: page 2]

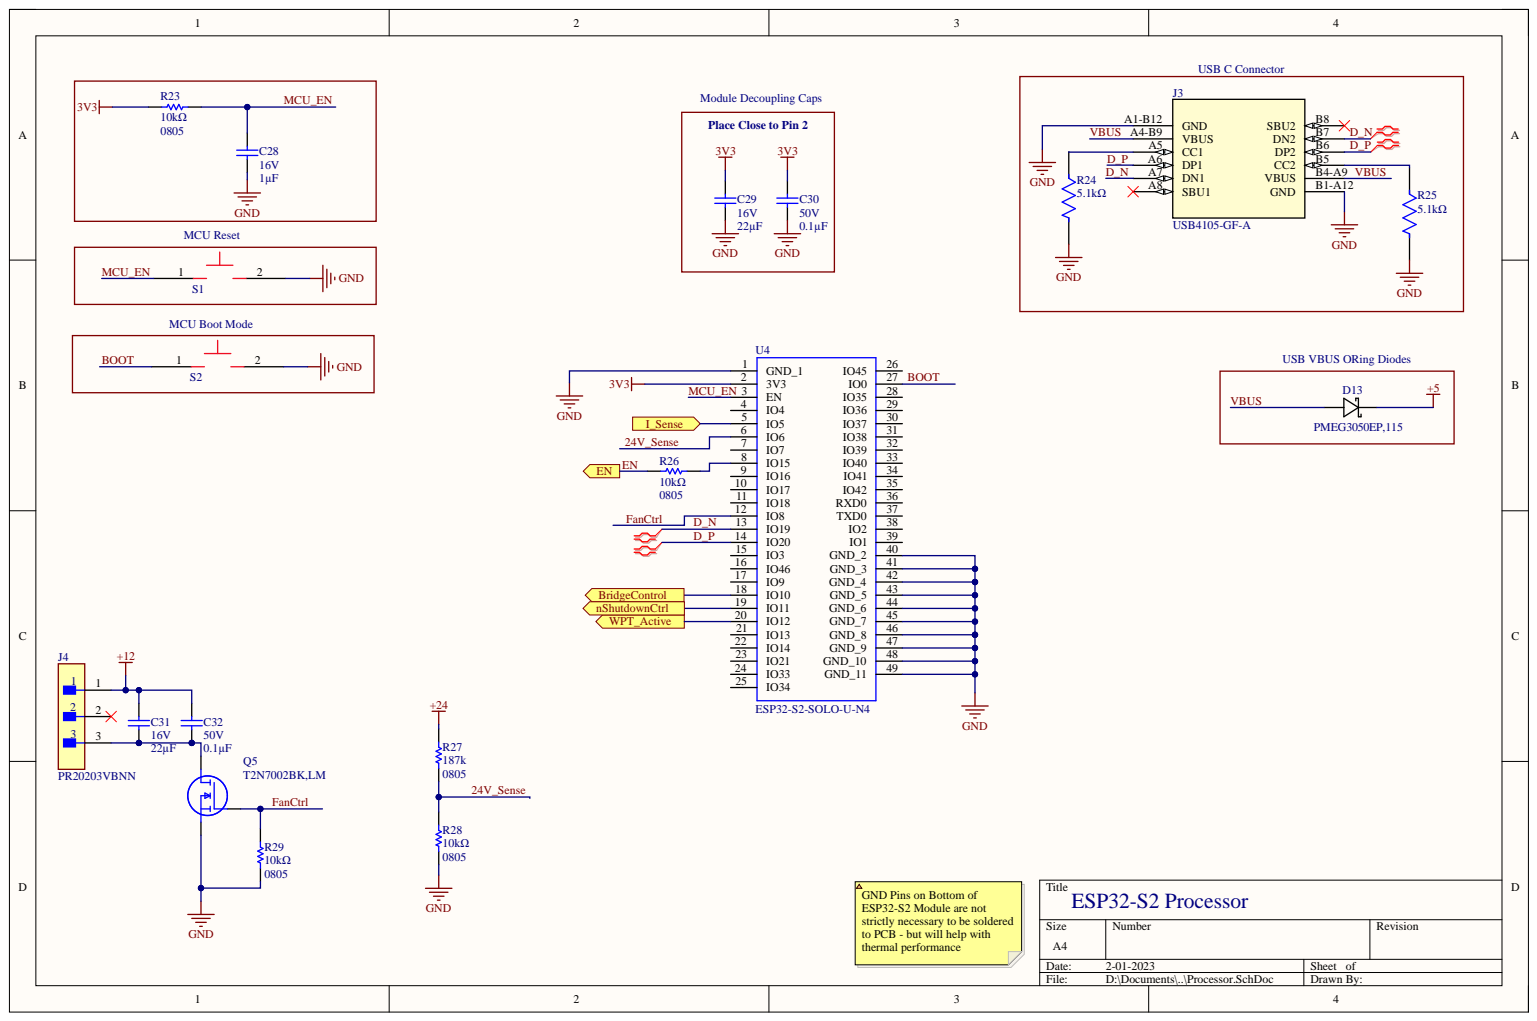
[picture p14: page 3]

Place Close to Pin 2 10kΩ

GND Pins on Bottom of
ESP32-S2 Module are not
strictly necessary to be soldered
to PCB - but will help with
thermal performance

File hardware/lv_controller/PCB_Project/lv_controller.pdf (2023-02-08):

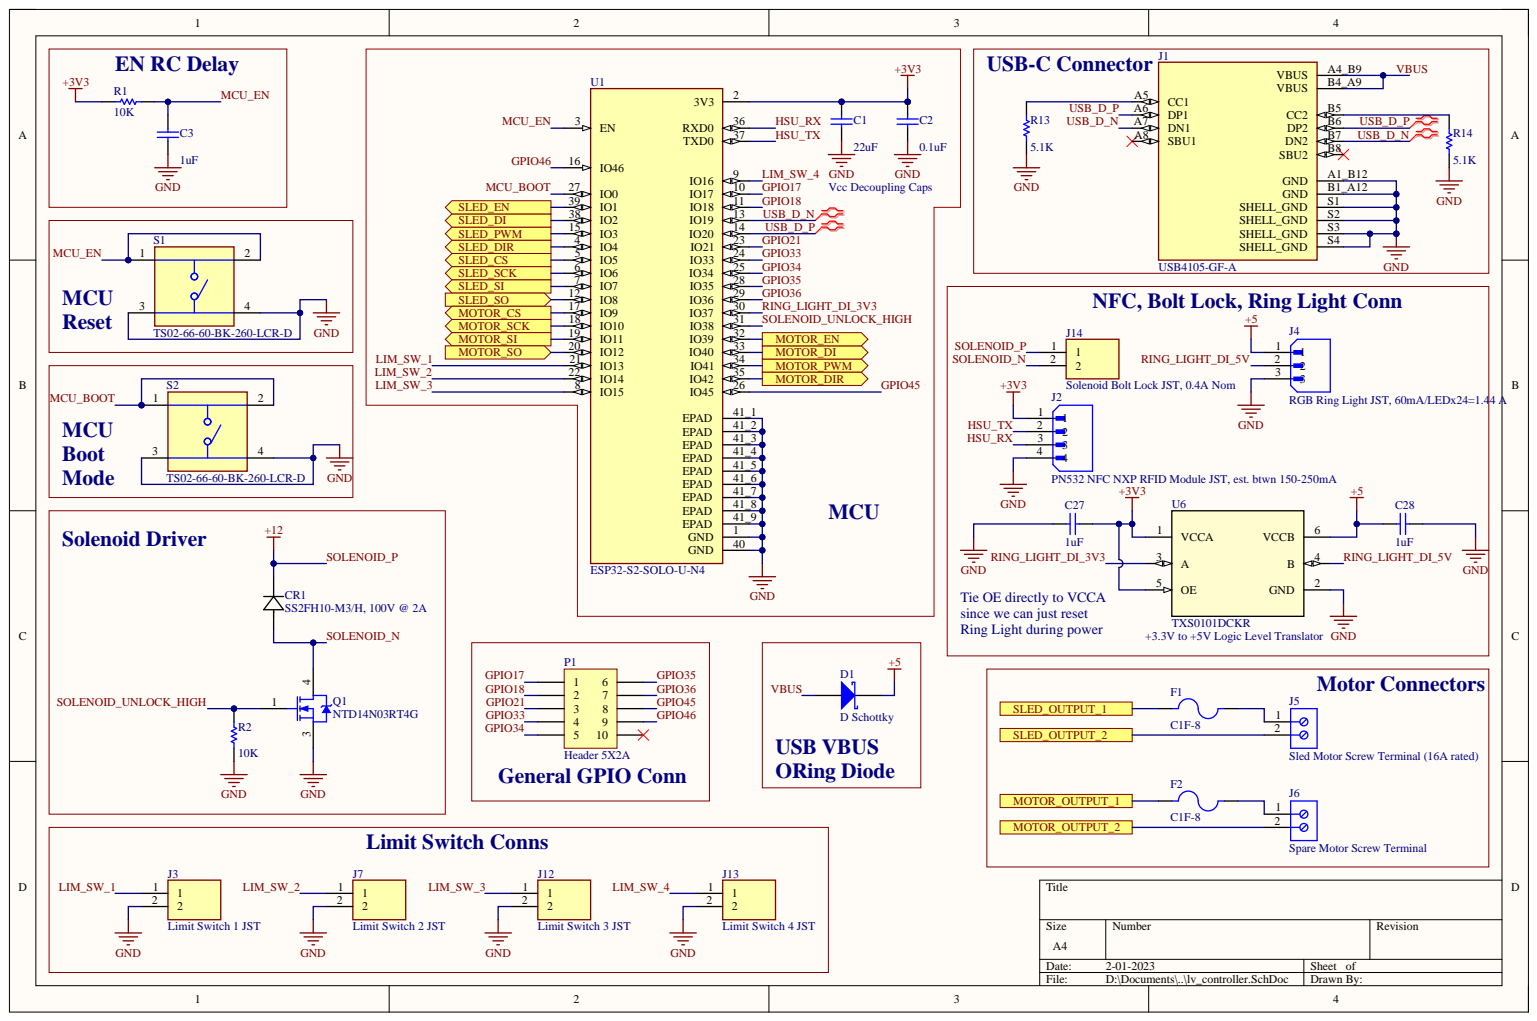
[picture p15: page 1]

NFC, Bolt Lock, Ring Light Conn

RGB Ring Light JST, 60mA/LEDx24=1.44 A

PN532 NFC NXP RFID Module JST, est. btwn 150-250mA

Tie OE directly to VCCA
since we can just reset
Ring Light during power

TXS0101DCKR
+3.3V to +5V Logic Level Translator GND

Sled Motor Screw Terminal (16A rated)

Spare Motor Screw Terminal

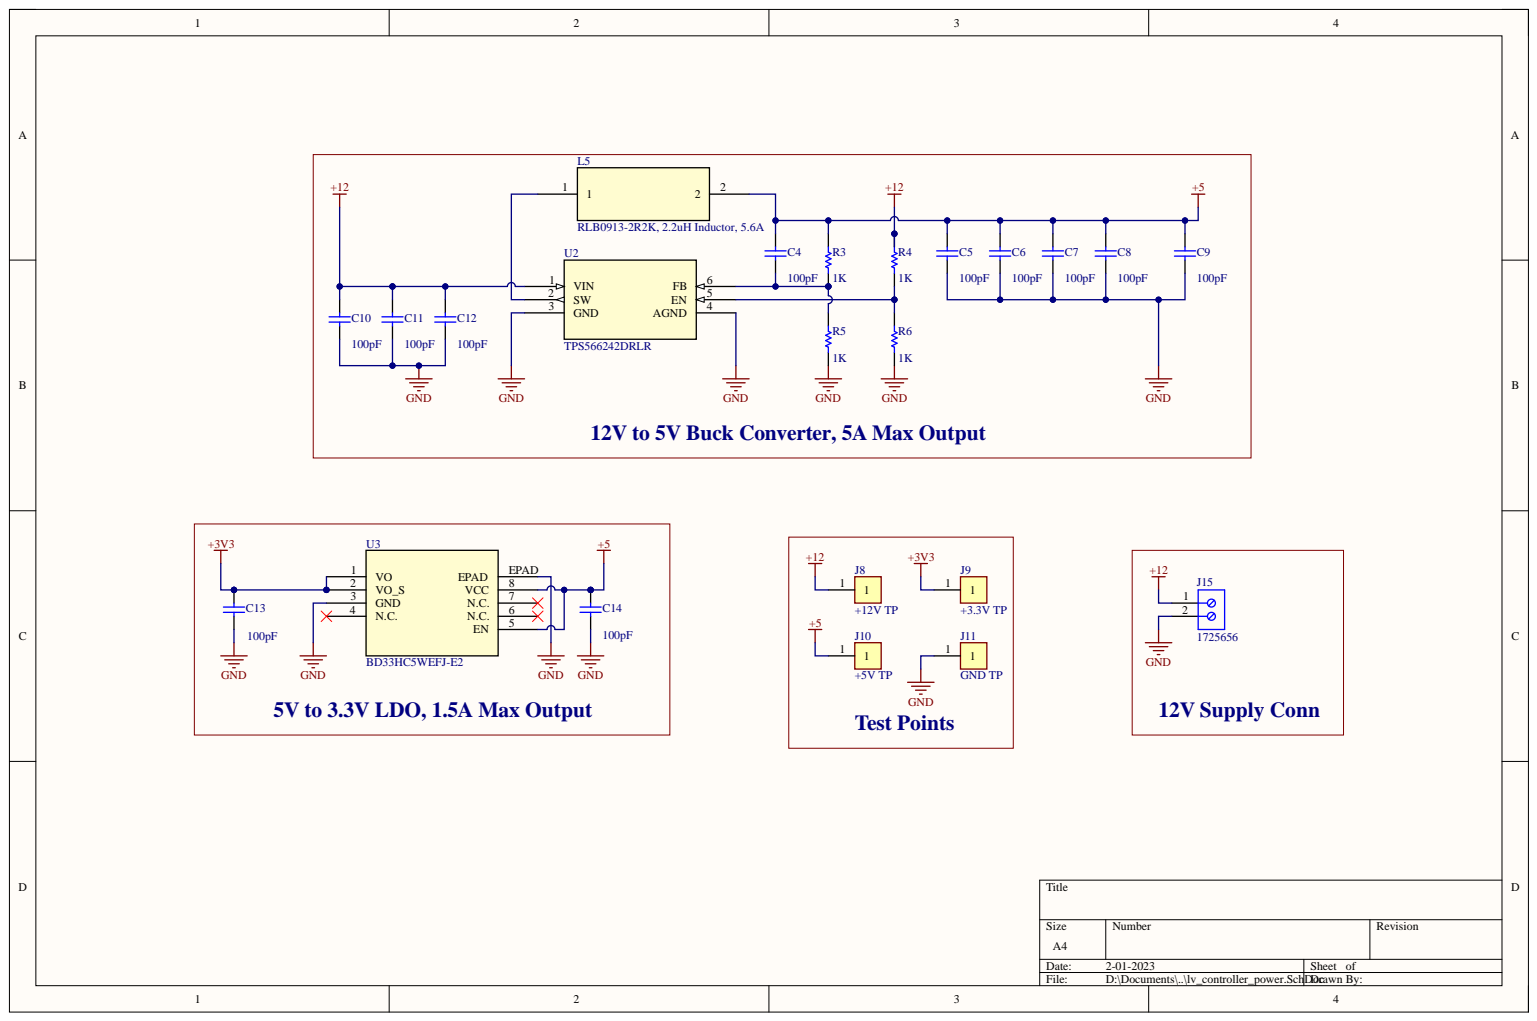
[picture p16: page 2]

12V to 5V Buck Converter, 5A Max Output

5V to 3.3V LDO, 1.5A Max Output

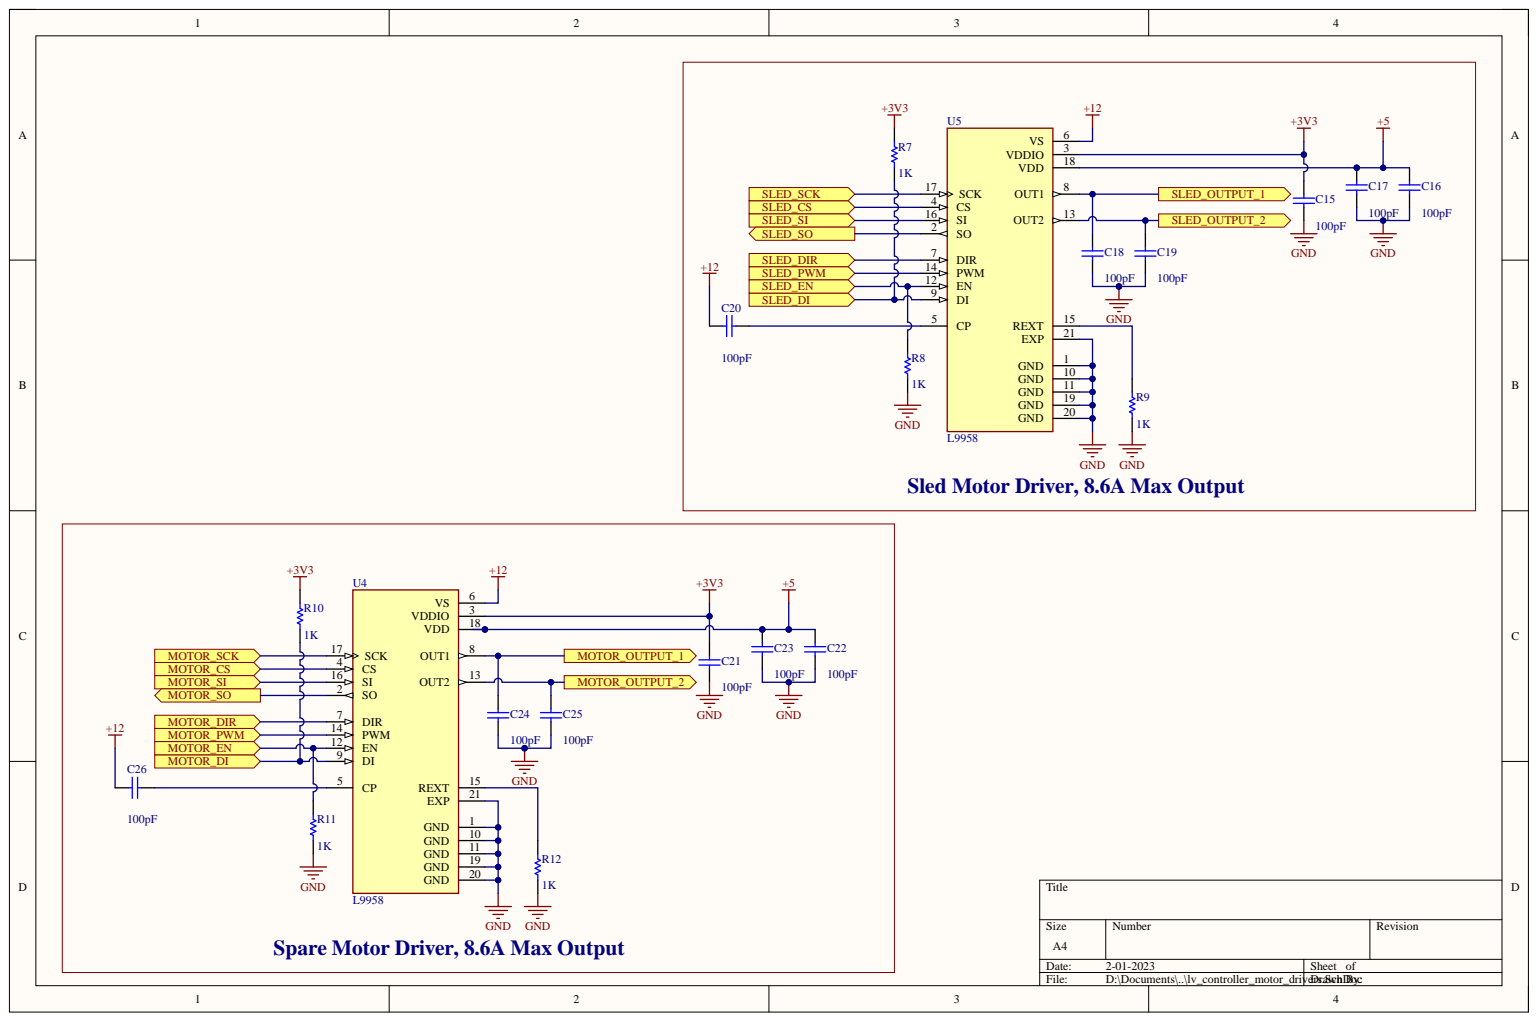
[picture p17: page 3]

Sled Motor Driver, 8.6A Max Output

DI 9 | GND

Spare Motor Driver, 8.6A Max Output

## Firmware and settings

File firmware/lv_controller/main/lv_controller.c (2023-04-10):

#include <stdio.h>
#include <stdbool.h>
#include <string.h>
#include <fcntl.h>

#include "freertos/FreeRTOS.h"
#include "freertos/task.h"
#include "freertos/queue.h"
#include "esp_log.h"
#include "esp_err.h"
#include "pn532.h"
#include "driver/gpio.h"
#include "driver/spi_master.h"
#include "driver/ledc.h"
#include "esp_system.h"
#include "esp_console.h"
#include "linenoise/linenoise.h"
#include "argtable3/argtable3.h"
#include "esp_vfs_cdcacm.h"
#include "nvs.h"
#include "nvs_flash.h"
#include "cmd_nvs.h"
#include "cmd_system.h"

#include "lv_controller.h"
#include "commands.h"
#include "nfc_module.h"
#include "ring_light.h"
#include "limit_switches.h"
#include "state_machine.h"

/* MACROS */
#define SENDER_HOST SPI2_HOST
#define PIN_NUM_MISO 12
#define PIN_NUM_MOSI 7
#define PIN_NUM_CLK 6
#define PIN_NUM_CS 5

/* GLOBALS */
static const char *TAG = "main";
TaskHandle_t nfc_module_task_handle = NULL;
TaskHandle_t state_machine_task_handle = NULL;

/* INITS */
static void init_GPIO(void)
{
    // Set solenoid output
    gpio_set_direction(GPIO_NUM_38, GPIO_MODE_OUTPUT);

    // Set limit switch inputs
    gpio_set_direction(LIM1_GPIO, GPIO_MODE_INPUT); // LIM1
    gpio_pulldown_dis(LIM1_GPIO);
    gpio_pullup_en(LIM1_GPIO);
    gpio_set_intr_type(LIM1_GPIO, GPIO_INTR_NEGEDGE);

    gpio_set_direction(LIM2_GPIO, GPIO_MODE_INPUT); // LIM2
    gpio_pulldown_dis(LIM2_GPIO);
    gpio_pullup_en(LIM2_GPIO);
    gpio_set_intr_type(LIM2_GPIO, GPIO_INTR_NEGEDGE);

    gpio_set_direction(LIM3_GPIO, GPIO_MODE_INPUT); // LIM3
    gpio_pulldown_dis(LIM3_GPIO);
    gpio_pullup_en(LIM3_GPIO);
    gpio_set_intr_type(LIM3_GPIO, GPIO_INTR_NEGEDGE);

    gpio_set_direction(LIM4_GPIO, GPIO_MODE_INPUT); // LIM4
    gpio_pulldown_dis(LIM4_GPIO);
    gpio_pullup_en(LIM4_GPIO);
    gpio_set_intr_type(LIM4_GPIO, GPIO_INTR_NEGEDGE);

    // Set sled control outputs
    gpio_set_direction(GPIO_NUM_1, GPIO_MODE_OUTPUT); // EN
    gpio_set_direction(GPIO_NUM_2, GPIO_MODE_OUTPUT); // DI
    gpio_set_direction(GPIO_NUM_3, GPIO_MODE_OUTPUT); // PWM
    gpio_set_direction(GPIO_NUM_4, GPIO_MODE_OUTPUT); // DIR
}

static void ledc_init(void)
{
    // Prepare and then apply the LEDC PWM timer configuration
    ledc_timer_config_t ledc_timer = {
        .speed_mode = LEDC_MODE,
        .timer_num = LEDC_TIMER_0,
        .duty_resolution = LEDC_TIMER_10_BIT,
        .freq_hz = 1000, // Set output frequency at 5 kHz
        .clk_cfg = LEDC_AUTO_CLK};
    ESP_ERROR_CHECK(ledc_timer_config(&ledc_timer));

    // Prepare and then apply the LEDC PWM channel configuration
    ledc_channel_config_t ledc_channel = {
        .speed_mode = LEDC_MODE,
        .channel = LEDC_CHANNEL_0,
        .timer_sel = LEDC_TIMER_0,
        .intr_type = LEDC_INTR_DISABLE,
        .gpio_num = LEDC_GPIO,
        .duty = 0, // Set duty to 0%
        .hpoint = 0};
    ESP_ERROR_CHECK(ledc_channel_config(&ledc_channel));
}

static void initialize_nvs(void)
{
    esp_err_t err = nvs_flash_init();
    if (err == ESP_ERR_NVS_NO_FREE_PAGES || err == ESP_ERR_NVS_NEW_VERSION_FOUND)
    {
        ESP_ERROR_CHECK(nvs_flash_erase());
        err = nvs_flash_init();
    }
    ESP_ERROR_CHECK(err);
}

static void initialize_console(void)
{
    /* Disable buffering on stdin */
    setvbuf(stdin, NULL, _IONBF, 0);

    /* Minicom, screen, idf_monitor send CR when ENTER key is pressed */
    esp_vfs_dev_cdcacm_set_rx_line_endings(ESP_LINE_ENDINGS_CR);
    /* Move the caret to the beginning of the next line on '\n' */
    esp_vfs_dev_cdcacm_set_tx_line_endings(ESP_LINE_ENDINGS_CRLF);

    /* Enable non-blocking mode on stdin and stdout */
    fcntl(fileno(stdout), F_SETFL, 0);
    fcntl(fileno(stdin), F_SETFL, 0);

    /* Initialize the console */
    esp_console_config_t console_config = {
        .max_cmdline_args = 8,
        .max_cmdline_length = 256,
#if CONFIG_LOG_COLORS
        .hint_color = atoi(LOG_COLOR_CYAN)
#endif
    };
    ESP_ERROR_CHECK(esp_console_init(&console_config));

    /* Configure linenoise line completion library */
    /* Enable multiline editing. If not set, long commands will scroll within
     * single line.
     */
    linenoiseSetMultiLine(1);

    /* Tell linenoise where to get command completions and hints */
    linenoiseSetCompletionCallback(&esp_console_get_completion);
    linenoiseSetHintsCallback((linenoiseHintsCallback *)&esp_console_get_hint);

    /* Set command history size */
    linenoiseHistorySetMaxLen(10);
}

/* REGISTER COMMANDS */
static void register_commands(void)
{
    /* Lock Solenoid */
    esp_console_cmd_t lock_solenoid_cmd = {
        .command = "lock_solenoid",
        .help = "Sets solenoid bolt to locked state",
        .hint = NULL,
        .func = lock_solenoid_comm,
        .argtable = NULL,
    };
    esp_err_t ret = esp_console_cmd_register(&lock_solenoid_cmd);
    if (ret != ESP_OK)
    {
        printf("Error resgistering 'lock_solenoid' command\n");
    }

    /* Unlock Solenoid */
    esp_console_cmd_t unlock_solenoid_cmd = {
        .command = "unlock_solenoid",
        .help = "Sets solenoid bolt to unlocked state",
        .hint = NULL,
        .func = unlock_solenoid_comm,
        .argtable = NULL,
    };
    ret = esp_console_cmd_register(&unlock_solenoid_cmd);
    if (ret != ESP_OK)
    {
        printf("Error resgistering 'unlock_solenoid' command\n");
    }

    /* Set Motor PWM */
    struct arg_int *duty;
    struct arg_end *end_pwm;
    void *set_pwm_argtable[] = {
        duty = arg_intn(NULL, NULL, "<duty>", 1, 2, "duty-cycle"),
        end_pwm = arg_end(10),
    };

    esp_console_cmd_t set_pwn_cmd = {
        .command = "set_pwm",
        .help = "Sets the duty cycle for PWM for the sled motor",
        .hint = NULL,
        .func = set_pwm,
        .argtable = set_pwm_argtable,
    };
    ret = esp_console_cmd_register(&set_pwn_cmd);
    if (ret != ESP_OK)
    {
        printf("Error resgistering 'set_pwn' command\n");
    }

    /* Set Motor DIR */
    struct arg_int *dir;
    struct arg_end *end_dir;
    void *set_dir_argtable[] = {
        dir = arg_intn(NULL, NULL, "<dir>", 1, 1, "direction of motor"),
        end_dir = arg_end(10),
    };

    esp_console_cmd_t set_mtr_dir_cmd = {
        .command = "set_mtr_dir",
        .help = "Sets the sled motor direction",
        .hint = NULL,
        .func = set_mtr_dir,
        .argtable = set_dir_argtable,
    };
    ret = esp_console_cmd_register(&set_mtr_dir_cmd);
    if (ret != ESP_OK)
    {
        printf("Error resgistering 'set_mtr_dir' command\n");
    }

    /* Enable Motor Output */
    esp_console_cmd_t en_mtr_output_cmd = {
        .command = "en_mtr_output",
        .help = "Enables the motor output",
        .hint = NULL,
        .func = enable_motor_output,
        .argtable = NULL,
    };
    ret = esp_console_cmd_register(&en_mtr_output_cmd);
    if (ret != ESP_OK)
    {
        printf("Error resgistering 'en_mtr_output' command\n");
    }

    /* Disable Motor Output */
    esp_console_cmd_t dis_mtr_output_cmd = {
        .command = "dis_mtr_output",
        .help = "Disables the motor output",
        .hint = NULL,
        .func = disable_motor_output,
        .argtable = NULL,
    };
    ret = esp_console_cmd_register(&dis_mtr_output_cmd);
    if (ret != ESP_OK)
    {
        printf("Error resgistering 'dis_mtr_output' command\n");
    }

    /* Start Rainbow Chase on Ring Light */
    esp_console_cmd_t rainbow_chase_start_cmd = {
        .command = "rainbow_chase_start",
        .help = "Start rRainbow chase on ring light",
        .hint = NULL,
        .func = rainbow_chase_start_comm,
        .argtable = NULL,
    };
    ret = esp_console_cmd_register(&rainbow_chase_start_cmd);
    if (ret != ESP_OK)
    {
        printf("Error resgistering 'rainbow_chase_start' command\n");
    }

    /* Stop Rainbow Chase on Ring Light */
    esp_console_cmd_t rainbow_chase_stop_cmd = {
        .command = "rainbow_chase_stop",
        .help = "Stop rainbow chase on ring light",
        .hint = NULL,
        .func = rainbow_chase_stop_comm,
        .argtable = NULL,
    };
    ret = esp_console_cmd_register(&rainbow_chase_stop_cmd);
    if (ret != ESP_OK)
    {
        printf("Error resgistering 'rainbow_chase_stop' command\n");
    }

    /* Set white LEDs on Ring Light */
    esp_console_cmd_t white_leds_cmd = {
        .command = "white_leds",
        .help = NULL,
        .hint = NULL,
        .func = set_white_leds,
        .argtable = NULL,
    };
    ret = esp_console_cmd_register(&white_leds_cmd);
    if (ret != ESP_OK)
    {
        printf("Error resgistering 'white_leds' command\n");
    }

    /* Turn LEDs off on Ring Light */
    esp_console_cmd_t leds_off_cmd = {
        .command = "leds_off",
        .help = NULL,
        .hint = NULL,
        .func = leds_off_comm,
        .argtable = NULL,
    };
    ret = esp_console_cmd_register(&leds_off_cmd);
    if (ret != ESP_OK)
    {
        printf("Error resgistering 'leds_off' command\n");
    }

    /* sled_out */
    esp_console_cmd_t sled_out_cmd = {
        .command = "sled_out",
        .help = NULL,
        .hint = NULL,
        .func = sled_out_comm,
        .argtable = NULL,
    };
    ret = esp_console_cmd_register(&sled_out_cmd);
    if (ret != ESP_OK)
    {
        printf("Error resgistering 'sled_out' state command\n");
    }

    /* sled_in */
    esp_console_cmd_t sled_in_cmd = {
        .command = "sled_in",
        .help = NULL,
        .hint = NULL,
        .func = sled_in_comm,
        .argtable = NULL,
    };
    ret = esp_console_cmd_register(&sled_in_cmd);
    if (ret != ESP_OK)
    {
        printf("Error resgistering 'sled_in' state command\n");
    }

    /* stop_sled */
    esp_console_cmd_t stop_sled_cmd = {
        .command = "stop_sled",
        .help = NULL,
        .hint = NULL,
        .func = stop_sled_comm,
        .argtable = NULL,
    };
    ret = esp_console_cmd_register(&stop_sled_cmd);
    if (ret != ESP_OK)
    {
        printf("Error resgistering 'stop_sled' state command\n");
    }

    /* Start Heartbeat on Ring Light */
    esp_console_cmd_t heartbeat_start_cmd = {
        .command = "heartbeat_start",
        .help = NULL,
        .hint = NULL,
        .func = heartbeat_start_comm,
        .argtable = NULL,
    };
    ret = esp_console_cmd_register(&heartbeat_start_cmd);
    if (ret != ESP_OK)
    {
        printf("Error resgistering 'heartbeat_start' command\n");
    }

    /* Stop Heartbeat on Ring Light */
    esp_console_cmd_t heartbeat_stop_cmd = {
        .command = "heartbeat_stop",
        .help = NULL,
        .hint = NULL,
        .func = heartbeat_stop_comm,
        .argtable = NULL,
    };
    ret = esp_console_cmd_register(&heartbeat_stop_cmd);
    if (ret != ESP_OK)
    {
        printf("Error resgistering 'heartbeat_stop' command\n");
    }

    /* ------------------STATE COMMANDS------------------ */
    /* to_unlockedem */
    esp_console_cmd_t to_unlockedem_cmd = {
        .command = "to_unlockedem",
        .help = NULL,
        .hint = NULL,
        .func = to_unlockedem_comm,
        .argtable = NULL,
    };
    ret = esp_console_cmd_register(&to_unlockedem_cmd);
    if (ret != ESP_OK)
    {
        printf("Error resgistering 'to_unlockedem' state command\n");
    }

    /* to_loading */
    esp_console_cmd_t to_loading_cmd = {
        .command = "to_loading",
        .help = NULL,
        .hint = NULL,
        .func = to_loading_comm,
        .argtable = NULL,
    };
    ret = esp_console_cmd_register(&to_loading_cmd);
    if (ret != ESP_OK)
    {
        printf("Error resgistering 'to_loading' state command\n");
    }

    /* to_closed */
    esp_console_cmd_t to_closed_cmd = {
        .command = "to_closed",
        .help = NULL,
        .hint = NULL,
        .func = to_closed_comm,
        .argtable = NULL,
    };
    ret = esp_console_cmd_register(&to_closed_cmd);
    if (ret != ESP_OK)
    {
        printf("Error resgistering 'to_closed' state command\n");
    }

    /* to_compvision */
    esp_console_cmd_t to_compvision_cmd = {
        .command = "to_compvision",
        .help = NULL,
        .hint = NULL,
        .func = to_compvision_comm,
        .argtable = NULL,
    };
    ret = esp_console_cmd_register(&to_compvision_cmd);
    if (ret != ESP_OK)
    {
        printf("Error resgistering 'to_compvision' state command\n");
    }

    /* to_charging */
    esp_console_cmd_t to_charging_cmd = {
        .command = "to_charging",
        .help = NULL,
        .hint = NULL,
        .func = to_charging_comm,
        .argtable = NULL,
    };
    ret = esp_console_cmd_register(&to_charging_cmd);
    if (ret != ESP_OK)
    {
        printf("Error resgistering 'to_charging' state command\n");
    }

    /* to_unlocked */
    esp_console_cmd_t to_unlocked_cmd = {
        .command = "to_unlocked",
        .help = NULL,
        .hint = NULL,
        .func = to_unlocked_comm,
        .argtable = NULL,
    };
    ret = esp_console_cmd_register(&to_unlocked_cmd);
    if (ret != ESP_OK)
    {
        printf("Error resgistering 'to_unlocked' state command\n");
    }

    /* to_unloading */
    esp_console_cmd_t to_unloading_cmd = {
        .command = "to_unloading",
        .help = NULL,
        .hint = NULL,
        .func = to_unloading_comm,
        .argtable = NULL,
    };
    ret = esp_console_cmd_register(&to_unloading_cmd);
    if (ret != ESP_OK)
    {
        printf("Error resgistering 'to_unloading' state command\n");
    }

    /* to_empty */
    esp_console_cmd_t to_empty_cmd = {
        .command = "to_empty",
        .help = NULL,
        .hint = NULL,
        .func = to_empty_comm,
        .argtable = NULL,
    };
    ret = esp_console_cmd_register(&to_empty_cmd);
    if (ret != ESP_OK)
    {
        printf("Error resgistering 'to_empty' state command\n");
    }
}

void app_main(void)
{
    ESP_LOGI(TAG, "LV Controller Starting");

    /* GPIO Init */
    init_GPIO();

    /* Ring Light Init */
    init_ring_light();

    /* PWM Init */
    gpio_set_direction(GPIO_NUM_17, GPIO_MODE_OUTPUT); // for debug PWM LED only
    ledc_init();

    /* USB CONSOLE */
    initialize_nvs();
    initialize_console();

    /* Register commands */
    esp_console_register_help_command();
    register_system_common();
    register_system_sleep();
    register_nvs();
    register_commands();

    /* L9958 Motor Driver SPI bus setup */ // TODO
    esp_err_t err;
    spi_device_handle_t spi;
    spi_bus_config_t buscfg = {
        .miso_io_num = PIN_NUM_MISO,
        .mosi_io_num = PIN_NUM_MOSI,
        .sclk_io_num = PIN_NUM_CLK,
        .quadwp_io_num = -1,
        .quadhd_io_num = -1};

    /* Prompt to be printed before each line.
     * This can be customized, made dynamic, etc.
     */
    const char *prompt = LOG_COLOR_I CONFIG_IDF_TARGET "> " LOG_RESET_COLOR;

    printf("\n ==============================================================\n");
    printf(" |                                                            |\n");
    printf(" |                ELOC LV CONTROLLER INTERFACE                |\n");
    printf(" |                                                            |\n");
    printf(" ==============================================================\n\n");

    /* Figure out if the terminal supports escape sequences */
    int probe_status = linenoiseProbe();
    if (probe_status)
    { /* zero indicates success */
        // printf("\n"
        //        "Your terminal application does not support escape sequences.\n"
        //        "Line editing and history features are disabled.\n"
        //        "On Windows, try using Putty instead.\n");
        linenoiseSetDumbMode(1);
#if CONFIG_LOG_COLORS
        /* Since the terminal doesn't support escape sequences,
         * don't use color codes in the prompt.
         */
        prompt = CONFIG_IDF_TARGET "> ";
#endif // CONFIG_LOG_COLORS
    }

    /* Turn LEDs off on startup */
    leds_off_comm(0, NULL);

    /* NFC Module Task */
    xTaskCreate(read_single_nfc_tag, "read_single_nfc_tag", 4096, NULL, 10, &nfc_module_task_handle);

    /* Limit Switches Task */
    init_limit_switches();

    /* State Machine Task */
    // xTaskCreate(state_machine, "state_machine", 4096, NULL, 10, &state_machine_task_handle);

    /* Main loop */
    while (true)
    {
        /* Get a line using linenoise.
         * The line is returned when ENTER is pressed.
         */
        char *line = linenoise(prompt);
        if (line == NULL)
        { /* Ignore empty lines */
            continue;
        }
        /* Add the command to the history */
        linenoiseHistoryAdd(line);

        /* Try to run the command */
        int ret;
        err = esp_console_run(line, &ret);
        if (err == ESP_ERR_NOT_FOUND)
        {
            printf("Unrecognized command\n");
        }
        else if (err == ESP_ERR_INVALID_ARG)
        {
            // command was empty
        }
        else if (err == ESP_OK && ret != ESP_OK)
        {
            printf("Command returned non-zero error code: 0x%x (%s)\n", ret, esp_err_to_name(ret));
        }
        else if (err != ESP_OK)
        {
            printf("Internal error: %s\n", esp_err_to_name(err));
        }
        /* linenoise allocates line buffer on the heap, so need to free it */
        linenoiseFree(line);
    }

    printf(TAG, "Error or end-of-input, terminating console\n");
    ESP_LOGE(TAG, "Error or end-of-input, terminating console");
    esp_console_deinit();
}

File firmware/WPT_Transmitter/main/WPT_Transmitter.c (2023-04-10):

#include <stdio.h>
#include "driver/gpio.h"
#include "driver/ledc.h"
#include "esp_log.h"
#include "freertos/FreeRTOS.h"
#include "freertos/task.h"

#include "inverter.h"
#include "v_sense.h"
#include "console.h"


void setup_gpio(void){
    gpio_reset_pin(V_INV_ENABLE_PIN);
    gpio_reset_pin(FAN_CTRL_PIN);
    gpio_reset_pin(BRIDGE_CTRL_PIN);
    gpio_reset_pin(NOT_SHUTDOWN_PIN);
    gpio_reset_pin(WPT_ACTIVE_LED_PIN);

    gpio_set_direction(V_INV_ENABLE_PIN, GPIO_MODE_OUTPUT);
    gpio_set_direction(FAN_CTRL_PIN, GPIO_MODE_OUTPUT);
    gpio_set_direction(BRIDGE_CTRL_PIN, GPIO_MODE_OUTPUT);
    gpio_set_direction(NOT_SHUTDOWN_PIN, GPIO_MODE_OUTPUT);
    gpio_set_direction(WPT_ACTIVE_LED_PIN, GPIO_MODE_OUTPUT);

    gpio_set_level(WPT_ACTIVE_LED_PIN, 1); // This turns off the LED
}

void app_main(void)
{
    setup_gpio();
    init_inverter();
    calibrate_adc();
    init_adc();
    
    turn_on_inv_rail();
    // turn_off_inv_rail();
    // printf("Setup Completed. Inverter Should be on");

    xTaskCreate(flash_wpt_led, "LED_blink_Task", 2500, NULL, 2, NULL);
    xTaskCreate(poll_adc_task, "V_monitor_task", 8000, NULL, 2, NULL);

    // Setup and start Console for user interaction
    initialize_nvs();
    initialize_console();
    run_console();
}

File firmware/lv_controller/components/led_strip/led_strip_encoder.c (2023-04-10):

/*
 * SPDX-FileCopyrightText: 2021-2022 Espressif Systems (Shanghai) CO LTD
 *
 * SPDX-License-Identifier: Apache-2.0
 */

#include "esp_check.h"
#include "led_strip_encoder.h"

static const char *TAG = "led_encoder";

typedef struct
{
    rmt_encoder_t base;
    rmt_encoder_t *bytes_encoder;
    rmt_encoder_t *copy_encoder;
    int state;
    rmt_symbol_word_t reset_code;
} rmt_led_strip_encoder_t;

static size_t rmt_encode_led_strip(rmt_encoder_t *encoder, rmt_channel_handle_t channel, const void *primary_data, size_t data_size, rmt_encode_state_t *ret_state)
{
    rmt_led_strip_encoder_t *led_encoder = __containerof(encoder, rmt_led_strip_encoder_t, base);
    rmt_encoder_handle_t bytes_encoder = led_encoder->bytes_encoder;
    rmt_encoder_handle_t copy_encoder = led_encoder->copy_encoder;
    rmt_encode_state_t session_state = 0;
    rmt_encode_state_t state = 0;
    size_t encoded_symbols = 0;
    switch (led_encoder->state)
    {
    case 0: // send RGB data
        encoded_symbols += bytes_encoder->encode(bytes_encoder, channel, primary_data, data_size, &session_state);
        if (session_state & RMT_ENCODING_COMPLETE)
        {
            led_encoder->state = 1; // switch to next state when current encoding session finished
        }
        if (session_state & RMT_ENCODING_MEM_FULL)
        {
            state |= RMT_ENCODING_MEM_FULL;
            goto out; // yield if there's no free space for encoding artifacts
        }
    // fall-through
    case 1: // send reset code
        encoded_symbols += copy_encoder->encode(copy_encoder, channel, &led_encoder->reset_code,
                                                sizeof(led_encoder->reset_code), &session_state);
        if (session_state & RMT_ENCODING_COMPLETE)
        {
            led_encoder->state = 0; // back to the initial encoding session
            state |= RMT_ENCODING_COMPLETE;
        }
        if (session_state & RMT_ENCODING_MEM_FULL)
        {
            state |= RMT_ENCODING_MEM_FULL;
            goto out; // yield if there's no free space for encoding artifacts
        }
    }
out:
    *ret_state = state;
    return encoded_symbols;
}

static esp_err_t rmt_del_led_strip_encoder(rmt_encoder_t *encoder)
{
    rmt_led_strip_encoder_t *led_encoder = __containerof(encoder, rmt_led_strip_encoder_t, base);
    rmt_del_encoder(led_encoder->bytes_encoder);
    rmt_del_encoder(led_encoder->copy_encoder);
    free(led_encoder);
    return ESP_OK;
}

static esp_err_t rmt_led_strip_encoder_reset(rmt_encoder_t *encoder)
{
    rmt_led_strip_encoder_t *led_encoder = __containerof(encoder, rmt_led_strip_encoder_t, base);
    rmt_encoder_reset(led_encoder->bytes_encoder);
    rmt_encoder_reset(led_encoder->copy_encoder);
    led_encoder->state = 0;
    return ESP_OK;
}

esp_err_t rmt_new_led_strip_encoder(const led_strip_encoder_config_t *config, rmt_encoder_handle_t *ret_encoder)
{
    esp_err_t ret = ESP_OK;
    rmt_led_strip_encoder_t *led_encoder = NULL;
    ESP_GOTO_ON_FALSE(config && ret_encoder, ESP_ERR_INVALID_ARG, err, TAG, "invalid argument");
    led_encoder = calloc(1, sizeof(rmt_led_strip_encoder_t));
    ESP_GOTO_ON_FALSE(led_encoder, ESP_ERR_NO_MEM, err, TAG, "no mem for led strip encoder");
    led_encoder->base.encode = rmt_encode_led_strip;
    led_encoder->base.del = rmt_del_led_strip_encoder;
    led_encoder->base.reset = rmt_led_strip_encoder_reset;
    // different led strip might have its own timing requirements, following parameter is for WS2812
    rmt_bytes_encoder_config_t bytes_encoder_config = {
        .bit0 = {
            .level0 = 1,
            .duration0 = 0.3 * config->resolution / 1000000, // T0H=0.3us
            .level1 = 0,
            .duration1 = 0.9 * config->resolution / 1000000, // T0L=0.9us
        },
        .bit1 = {
            .level0 = 1,
            .duration0 = 0.9 * config->resolution / 1000000, // T1H=0.9us
            .level1 = 0,
            .duration1 = 0.3 * config->resolution / 1000000, // T1L=0.3us
        },
        .flags.msb_first = 1 // WS2812 transfer bit order: G7...G0R7...R0B7...B0
    };
    ESP_GOTO_ON_ERROR(rmt_new_bytes_encoder(&bytes_encoder_config, &led_encoder->bytes_encoder), err, TAG, "create bytes encoder failed");
    rmt_copy_encoder_config_t copy_encoder_config = {};
    ESP_GOTO_ON_ERROR(rmt_new_copy_encoder(&copy_encoder_config, &led_encoder->copy_encoder), err, TAG, "create copy encoder failed");

    uint32_t reset_ticks = config->resolution / 1000000 * 50 / 2; // reset code duration defaults to 50us
    led_encoder->reset_code = (rmt_symbol_word_t){
        .level0 = 0,
        .duration0 = reset_ticks,
        .level1 = 0,
        .duration1 = reset_ticks,
    };
    *ret_encoder = &led_encoder->base;
    return ESP_OK;
err:
    if (led_encoder)
    {
        if (led_encoder->bytes_encoder)
        {
            rmt_del_encoder(led_encoder->bytes_encoder);
        }
        if (led_encoder->copy_encoder)
        {
            rmt_del_encoder(led_encoder->copy_encoder);
        }
        free(led_encoder);
    }
    return ret;
}

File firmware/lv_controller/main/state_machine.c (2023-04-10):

#include <stdio.h>
#include <string.h>

#include "freertos/FreeRTOS.h"
#include "freertos/task.h"
#include "freertos/queue.h"
#include "driver/gpio.h"
#include "esp_log.h"

#include "state_machine.h"
#include "motor.h"
#include "limit_switches.h"
#include "ring_light.h"
#include "solenoid.h"

enum states
{
    UnlockedEm,
    Loading,
    Closed,
    CompVision,
    Charging,
    Unlocked,
    Unloading,
    Empty,
    Vacant,
    BADKEY = -1
};

static const char *TAG = "state_machine";
static enum states curr_state = Vacant;

int to_unlockedem(void)
{
    // Start a heartbeat on the ring light in prep for loading
    heartbeat_start();

    // Unlock door
    unlock_solenoid();

    // Poll until limit switch is de-pressed for DOOR is OPEN (LIM4)
    LIM4_state = get_lim_switch_curr_value(LIM4_GPIO);
    while (!LIM4_state)
    {
        LIM4_state = get_lim_switch_curr_value(LIM4_GPIO);
        vTaskDelay(pdMS_TO_TICKS(100));
    }

    // Lock solenoid to prevent overheating
    printf("Locking solenoid...\n");
    lock_solenoid();

    // Set new state
    printf("UNLOCKEDEM_state\n");
    curr_state = UnlockedEm;
    return 0;
}

int to_loading(void)
{
    // Move sled out
    sled_out();

    printf("Waiting for LIM1 (SLED OUT)...\n");
    // Poll until limit switch is hit for SLED OUT (LIM1), then stop the sled (LIM1)
    LIM1_state = get_lim_switch_curr_value(LIM1_GPIO);
    while (LIM1_state)
    {
        LIM1_state = get_lim_switch_curr_value(LIM1_GPIO);
        vTaskDelay(pdMS_TO_TICKS(100));
    }

    printf("Stopping sled...\n");
    // Stop sled
    stop_sled();

    // Set new state
    printf("LOADING_state\n");
    curr_state = Loading;
    return 0;
}

int to_closed(void)
{
    // Move sled in
    printf("Moving sled in...\n");
    sled_in();

    // Poll until limit switch is hit for SLED IN, then stop the sled (LIM3)
    LIM3_state = get_lim_switch_curr_value(LIM3_GPIO);
    while (LIM3_state)
    {
        LIM3_state = get_lim_switch_curr_value(LIM3_GPIO);
        vTaskDelay(pdMS_TO_TICKS(100));
    }
    printf("Stopping sled...\n");
    stop_sled();

    // Poll until limit switch is hit for DOOR CLOSED
    LIM4_state = get_lim_switch_curr_value(LIM4_GPIO);
    while (LIM4_state)
    {
        LIM4_state = get_lim_switch_curr_value(LIM4_GPIO);
        vTaskDelay(pdMS_TO_TICKS(100));
    }

    // Set new state
    printf("CLOSED_state\n");
    curr_state = Closed;
    return 0;
}

int to_compvision(void)
{
    // Turn off heartbeat from loading
    heartbeat_stop();
    vTaskDelay(pdMS_TO_TICKS(100)); // give the ring light some time to settle

    // Turn LEDs on white for CV
    white_leds();

    // Set new state
    printf("COMPVISION_state\n");
    curr_state = CompVision;
    return 0;
}

int to_charging(void)
{
    // Turn on rainbow chase for charging
    rainbow_chase_start();

    // Set new state
    printf("CHARGING_state\n");
    curr_state = Charging;
    return 0;
}

int to_unlocked(void)
{
    // Stop rainbow chase
    rainbow_chase_stop();

    // Turn LEDs off
    leds_off();

    // Start a heartbeat on the ring light for unloading
    heartbeat_start();

    // Unlock door
    unlock_solenoid();

    // Poll until limit switch is de-pressed for DOOR is OPEN (LIM4)
    LIM4_state = get_lim_switch_curr_value(LIM4_GPIO);
    while (!LIM4_state)
    {
        LIM4_state = get_lim_switch_curr_value(LIM4_GPIO);
        vTaskDelay(pdMS_TO_TICKS(100));
    }

    // Lock solenoid to prevent overheating
    lock_solenoid();

    // Set new state
    printf("UNLOCKED_state\n");
    curr_state = Unlocked;
    return 0;
}

int to_unloading(void)
{
    // Move sled out
    sled_out();

    // Poll until limit switch is hit for SLED OUT, then stop the sled (LIM1)
    LIM1_state = get_lim_switch_curr_value(LIM1_GPIO);
    while (LIM1_state)
    {
        LIM1_state = get_lim_switch_curr_value(LIM1_GPIO);
        vTaskDelay(pdMS_TO_TICKS(100));
    }

    // Stop sled
    stop_sled();

    // Set new state
    printf("UNLOADING_state\n");
    curr_state = Unloading;
    return 0;
}

int to_empty(void)
{
    // Move sled in
    sled_in();

    // Poll until limit switch is hit for SLED IN, then stop the sled (LIM3)
    LIM3_state = get_lim_switch_curr_value(LIM3_GPIO);
    while (LIM3_state)
    {
        LIM3_state = get_lim_switch_curr_value(LIM3_GPIO);
        vTaskDelay(pdMS_TO_TICKS(100));
    }

    // Stop the sled
    stop_sled();

    // Poll until limit switch is pressed for DOOR is CLOSED (LIM4)
    LIM4_state = get_lim_switch_curr_value(LIM4_GPIO);
    while (LIM4_state)
    {
        LIM4_state = get_lim_switch_curr_value(LIM4_GPIO);
        vTaskDelay(pdMS_TO_TICKS(100));
    }

    // Turn off heartbeat from unloading
    heartbeat_stop();

    // Set new state
    printf("EMPTY_state\n");
    curr_state = Empty;
    return 0;
}

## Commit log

2022-11-25 camera calibration images
2023-01-17 Add lv controller project
    [5000.SchLib, B2B-XH-A(LF)(SN).SchLib, B3B-XH-A(LF)(SN).SchLib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]
2023-01-18 Added Transmitter and Receiver PCBs
    [ELOC_Receiver.PrjPcb, ELOC_Transmitter.PrjPcb, Full_Bridge_Inverter.SchDoc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]
2023-01-18 Update PCB with minor changes
    [lv_controller.PcbDoc]
2023-01-18 Round PCB corners
    [lv_controller.PcbDoc]
2023-01-19 Remove date from LV controller
    [lv_controller.PcbDoc]
2023-01-20 Gerber Generation
2023-02-07 Uploaded PDF schematics + BOM for WPT boards
    [ELOC_Receiver_BOM.xlsx, ELOC_Transmitter_BOM.xlsx]
2023-02-08 Setup most functionality for transmitter board. Need to deal with ADC stuff next. Also Added .gitignore
2023-02-12 starting on ADC things
2023-02-12 Flash WPT LED for debug
2023-02-14 LEDC PWM generation working well!
2023-02-14 ADC continuous mode almost working
2023-02-15 ADC continuous mode working but calibration is funky
2023-02-16 Serial communication and stepper motor commands
2023-02-17 Add firmware for NFC, solenoid, and sled motor
2023-02-22 some calibration, some extra inverter funcs for frequency sweep
2023-02-22 calibration and marker detection with webcam
2023-02-24 gantry and vision calculations
2023-02-24 Added frequency sweep command. Improved ADC functionality slightly
2023-02-26 Added start and stop charging commands
2023-03-07 add to gantry util
2023-03-07 new camera calibration
2023-03-07 Add motor state commands
2023-03-20 Changed charging sw frequency for wacky man
2023-03-22 Add updates from further limit switch testing
2023-03-22 Add fixes from ring light heartbeat and sled movement
    [limit_switches.c, ring_light.c, ring_light.h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]
2023-03-24 Update brightness for ring light and lim switch bug fix
    [ring_light.c, state_machine.c]
